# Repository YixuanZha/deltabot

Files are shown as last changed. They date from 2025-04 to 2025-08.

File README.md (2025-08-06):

# The Delta Bot

### What is the Delta Bot?
The Delta Bot is an open-source DIY robot AI platform that uses Radxa's single board computer, the [Rock 5B](https://radxa.com/products/rock5/5b/), a simple [camera module](https://www.raspberrypi.com/products/camera-module-v2/), Parallax's [Continuous Rotation Servo Motors](https://www.parallax.com/product/parallax-continuous-rotation-servo-factory-centered/), and the [RPLIDAR A1](https://www.slamtec.com/en/lidar/a1), a LIDAR camera by Slamtec.

<p align="center">
  b465403a364265f6c7dfb5f9f959081e
</p>

### Purpose & Vision

<p align="center">
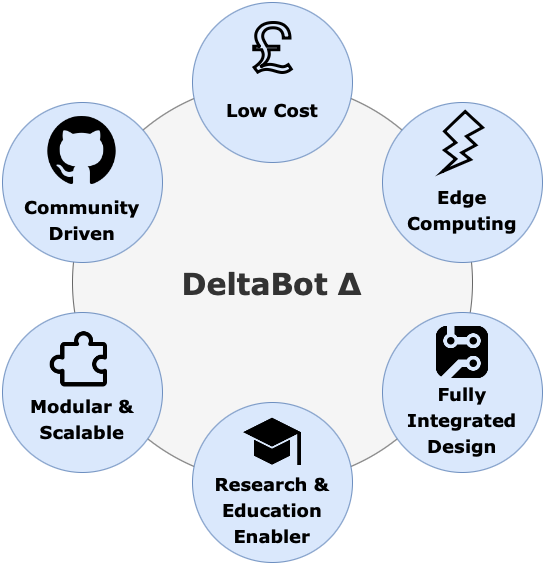
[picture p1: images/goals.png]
Goals
  
</p>

### What can it do?

- 360 Degree 2D LiDAR Scans
- Precise Servo Movement 
- 1080p Video Capture
- Can be configured for Line Following, SLAM, Obstacle Detection, and more!

### Video Demonstration

*A video demonstration will be added once mechanical repairs are complete.*

<p align="center">
  <a href="https://www.youtube.com/watch?v=VIDEO_ID">
    Watch the video
  </a>
</p>

## How to get started
- For the list of components used refer to [List.md](List.md).
- To first set up your RADXA ROCK5B computer, and configure its GPIO pins refer to [Setup.md](Setup.md).
- For details on the DeltaBot schematic, pcb, and footprint library refer to [PCB.md](PCB.md).

### Installing core tools
```bash
sudo apt install libopencv-dev opencv-data python3-opencv
sudo apt install opencl-headers ocl-icd-opencl-dev
sudo apt install libgstreamer1.0-dev gstreamer1.0-plugins-base gstreamer1.0-plugins-good gstreamer1.0-tools
```
### Build the project
```bash
mkdir build
cd build
cmake ..
make
```

### Run the tests
If you want to test the wheels
```bash
./TestServoMotor <left_speed> <right_speed>
```
- `<left_speed>`: Speed value for the left servo motor(-10~10)
- `<right_speed>`: Speed value for the right servo motor(-10~10)
- `speed range`: -10 is full speed counterclockwise, 10 is full speed clockwise, 0 is no rotation
or
```bash
./TestSpeedChange
```
This test will demonstrate the motors accelerating, decelerating, and stopping automatically.

If you want to test the robot's movement
```bash
./TestBotMotion
```
This test allows you to control a robot using your keyboard in a terminal environment. You can drive the robot forward, backward, turn, adjust speed, stop, and exit the program using designated keys.
#### Controls
| Key | Action |
|-----|---|
| W | Forward |
| S | Backward |
| A | Turn Left |
| D | Turn Right |
| R | Speed Up |
| F | Decelerate |
| X | Stop |
| Z | Quit |

#### Example

```text
Use the keyboard to control the bot: W(forward) S(backward) A(turn left) D(turn right) R(speed up) F(decelerate) X(stop) Z(quit)
Forward.....The speed is: 3
Turn left.....The speed is: 3
Speed up.....The speed is: 4
Stop.....
Quit.....
```
### Run the executable
```bash
./TestLineFollowing
```
You need to place the robot in a well-lit area with a high-contrast black line (e.g., electrical tape) on a white or light-colored background. The robot will then start its autonomous line-following behavior.

## Structure
The following outlines the DeltaBot's Architecture:
<p align="center">
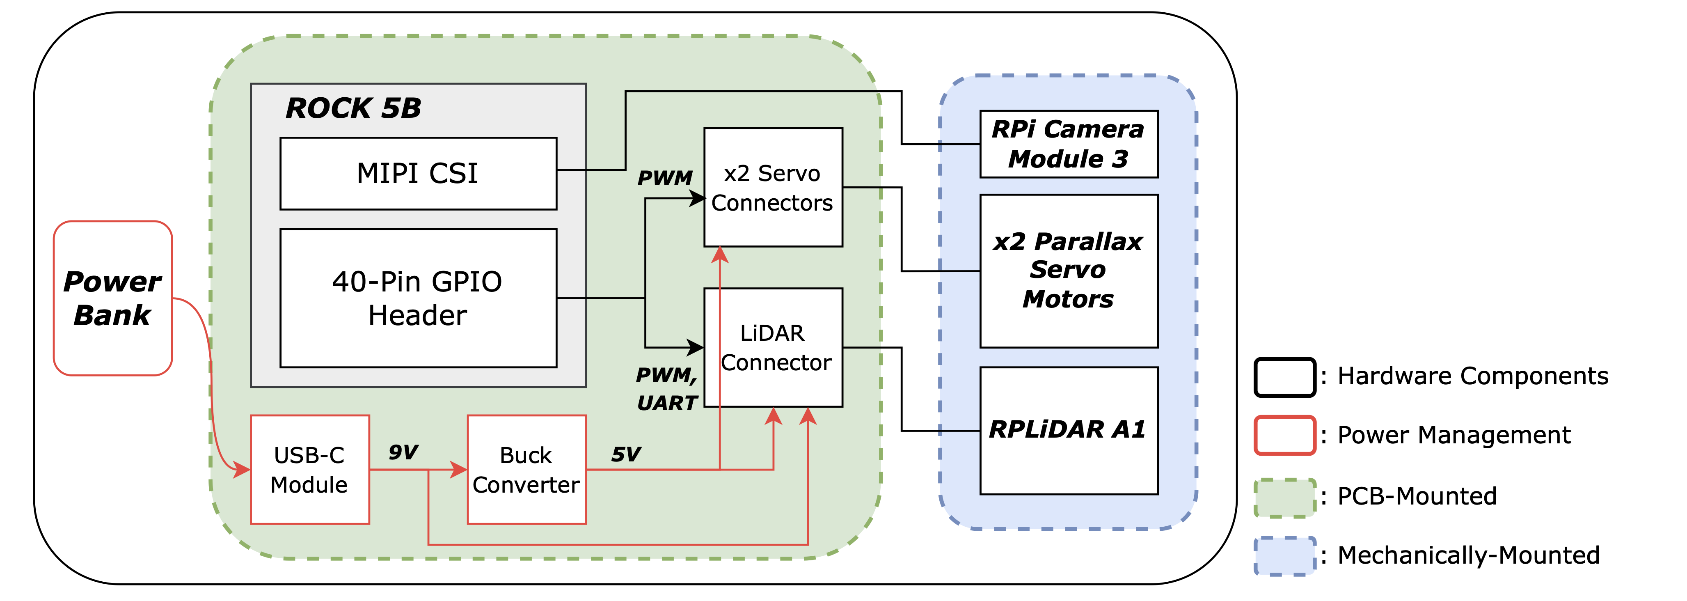
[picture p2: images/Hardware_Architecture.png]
  
</p>

### Additional Mechanical Parts
Additional Mechanical Parts were designed in CAD and can be accessed [here](additional_files/deltabot.f3z).
These were used to secure the external components onto the Single PCB Chassis:
<p align="center">
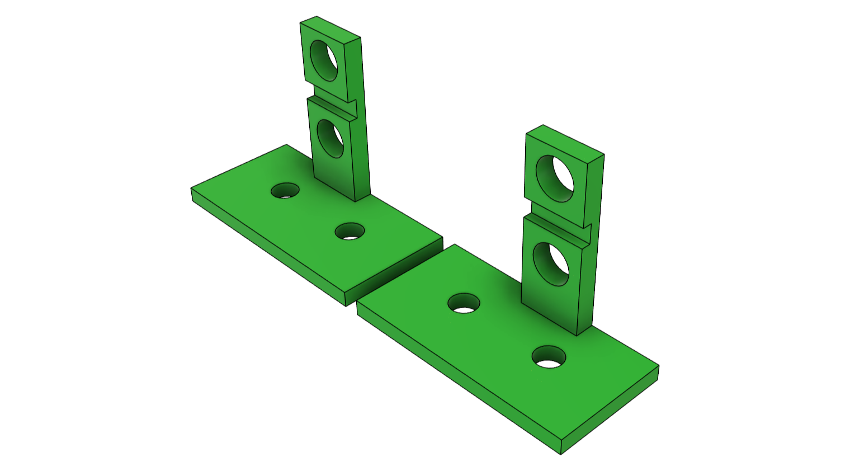
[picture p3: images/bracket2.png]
  
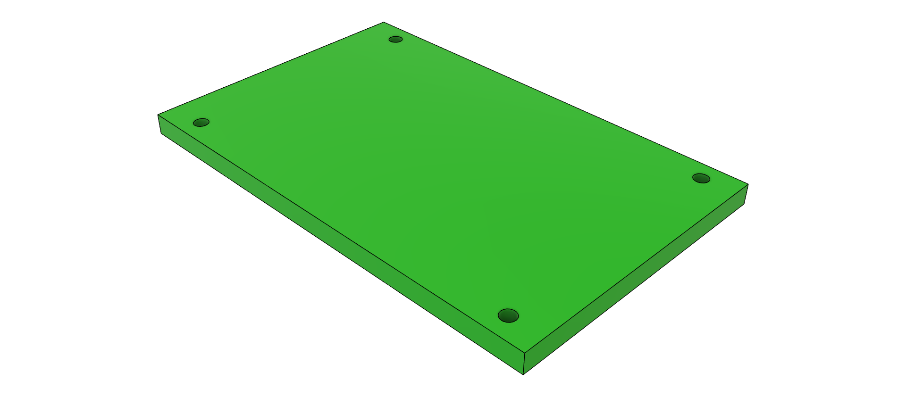
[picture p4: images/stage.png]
  
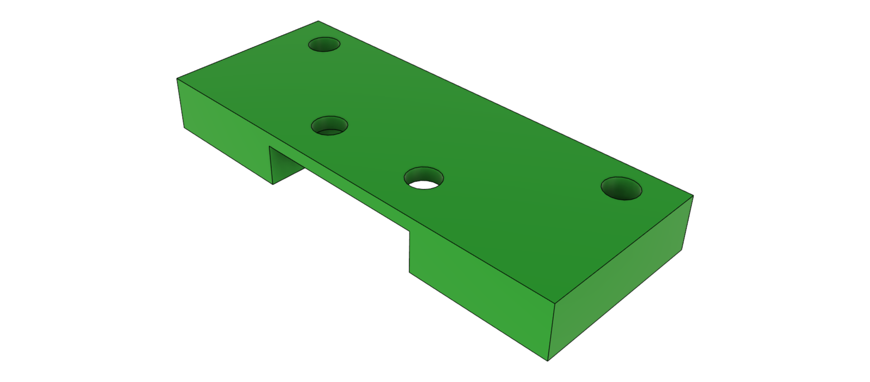
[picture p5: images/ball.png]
  
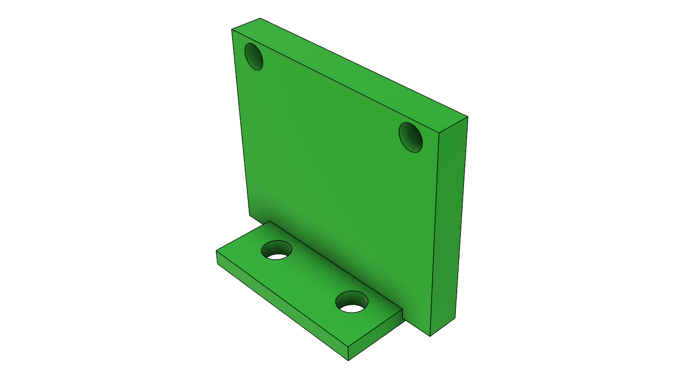
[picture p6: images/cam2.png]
  
</p>

## Further Documentation
- [RADXA ROCK 5B Geekbenchv6 CPU Results](https://browser.geekbench.com/v6/cpu/11503510)
- [RADXA ROCK 5B Geekbenchv6 GPU (OpenCL) Results](https://browser.geekbench.com/v6/compute/4045302)
- Scripts from rplidar_rock file were adopteed from [here.](https://github.com/berndporr/rplidar_rpi)

## Credits
- Saleh AlMulla - 2721704A@student.gla.ac.uk
- Bernd Porr -  bernd.porr@glasgow.ac.uk
- Yixuan Zha - 2974642Z@student.gla.ac.uk

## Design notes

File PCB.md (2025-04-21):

# DeltaBot PCB Overview

The DeltaBot PCB was designed in **KiCad** with a double-sided layer layout. The design integrates key subsystems including the **Radxa ROCK 5B**, LiDAR sensor, camera module, and servo motors.

<p align="center">
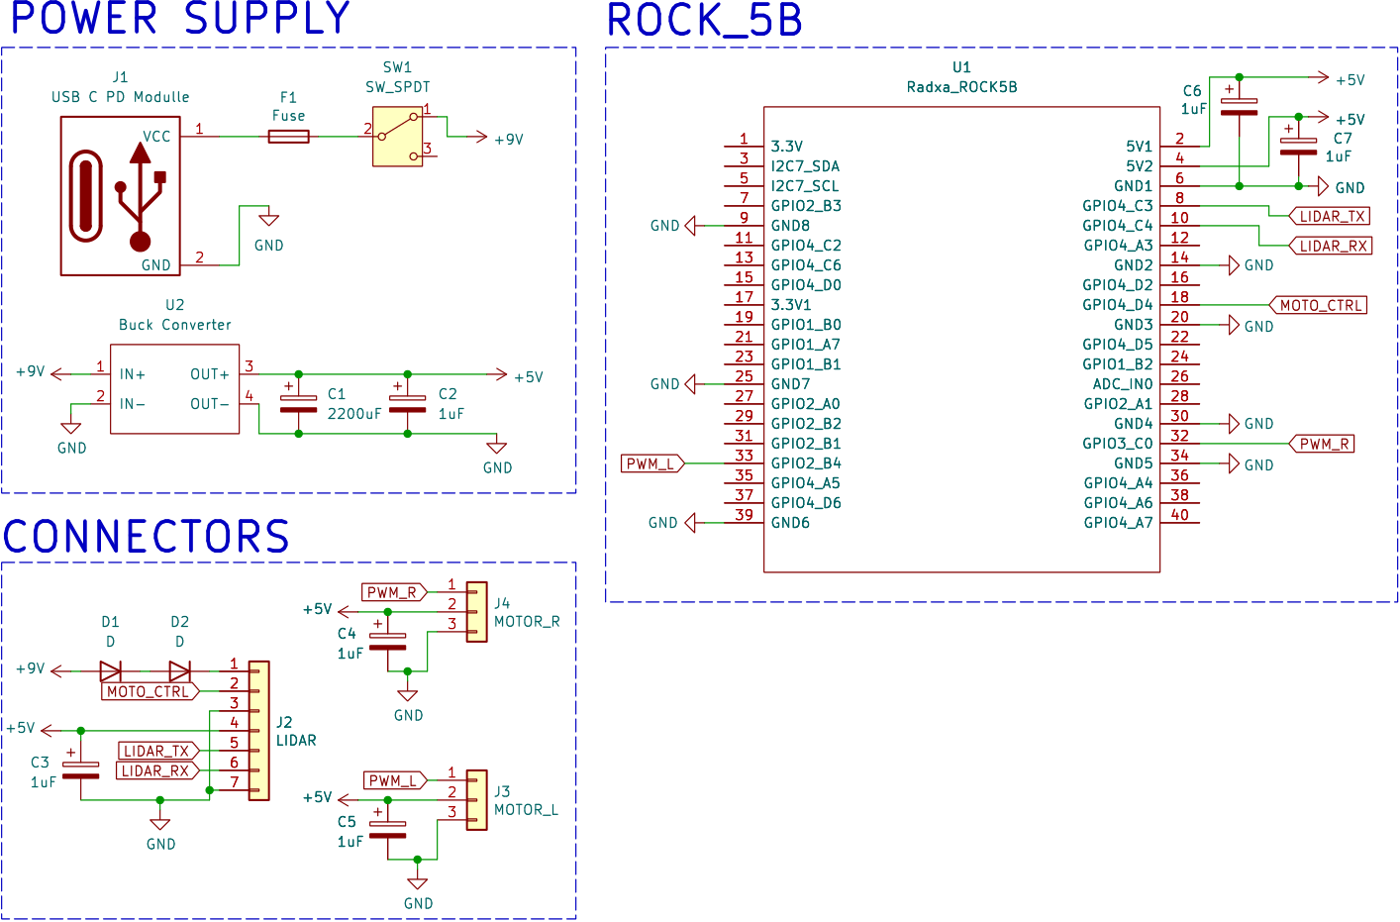
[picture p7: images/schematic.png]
  
</p>

---

## Power System
- Powered via **USB-C Power Delivery (PD)** module at **9V**, stepped down to **5V** using a **DC-DC buck converter**
- A **3.15A fuse** protects against overcurrent
- An **SPDT switch** provides manual ON/OFF control
- A **2200 µF capacitor** suppresses 5V rail ripple for improved voltage stability
- **1 uF** blocking capacitors between each POWER & GND

The following summarizes the power distribution architecture:

<p align="center">
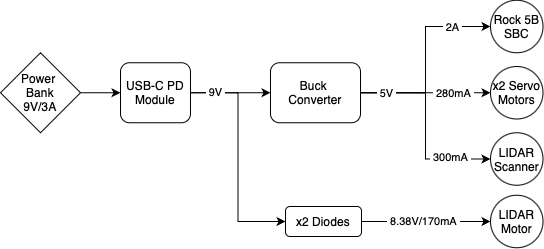
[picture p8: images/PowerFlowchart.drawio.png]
  
</p>

_Note: Current draw listed is based on peak operational requirements._

---

## PCB Layout (Front & Back Layers)

<p align="center">
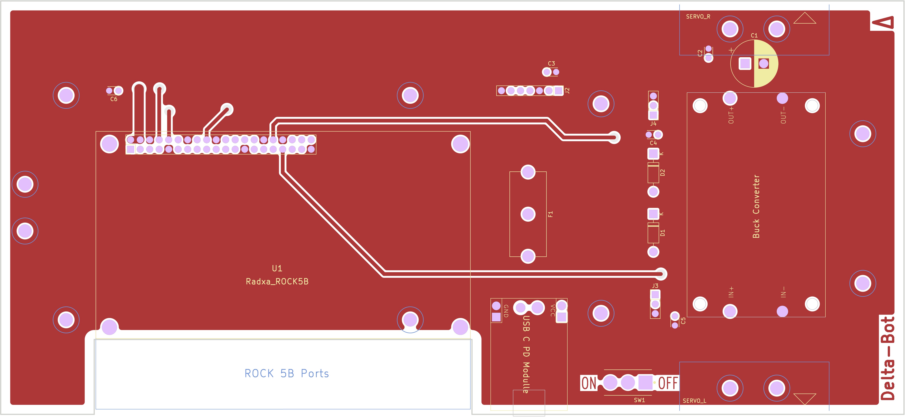
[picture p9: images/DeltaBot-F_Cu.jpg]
  
</p>
<p align="center">
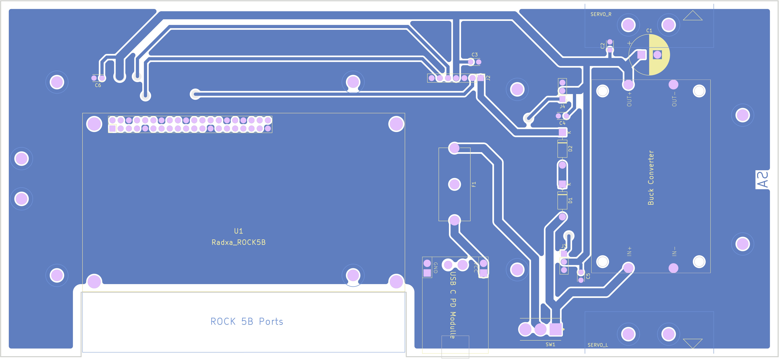
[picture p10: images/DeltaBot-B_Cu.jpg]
  
</p>

---

## ROCK 5B GPIO Pin Assignments

| Function | GPIO Pin(s) | Description |
|---|---|---|
| +5V Power | 2, 4 | Supplies power to board |
| GND | Multiple | Ground reference |
| UART_TX | 8 | TX to LiDAR's RX |
| UART_RX | 10 | RX from LiDAR's TX |
| MOTO_CTRL | 18 | PWM for LiDAR motor |
| PWM_L | 32 | PWM control for left servo |
| PWM_R | 33 | PWM control for right servo |

To change or add to the layout, check [here](https://wiki.radxa.com/Rock5/hardware/5b/gpio) for the rock's gpio connections.

---

## Connectors

- **J2 (LiDAR)**: 7-pin Molex  
  - UART (TX/RX), PWM for motor control, 5V & 8.34V power lines
  - There is a useful image on the LiDAR wiring in the read.me of [this repository](https://github.com/berndporr/rplidar_rpi).
- **J3 / J4 (Servo Motors)**: 3-pin headers  
  - 5V, GND, PWM (Left/Right)

---

## Files

- [Full Schematic](schematic_files/DeltaBot.kicad_sch)
- [PCB Design](schematic_files/DeltaBot.kicad_pcb)
- [PCB Footprints](schematic_files/deltabot.pretty.zip)
- [Rock 5B KiCAD Symbol](schematic_files/deltabot.lib.kicad_sym)
  
---

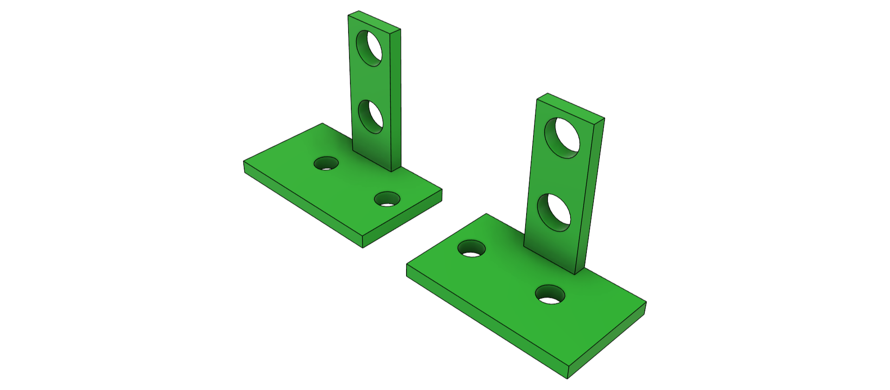
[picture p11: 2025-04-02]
images/bracket.png

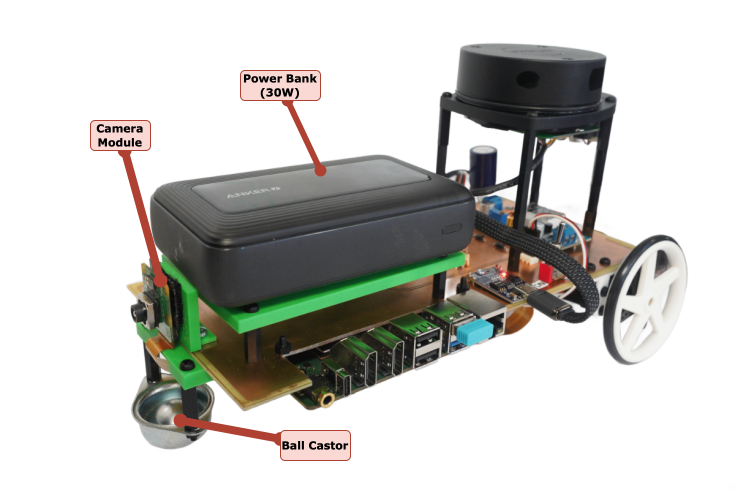
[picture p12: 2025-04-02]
images/frontbot.drawio.png

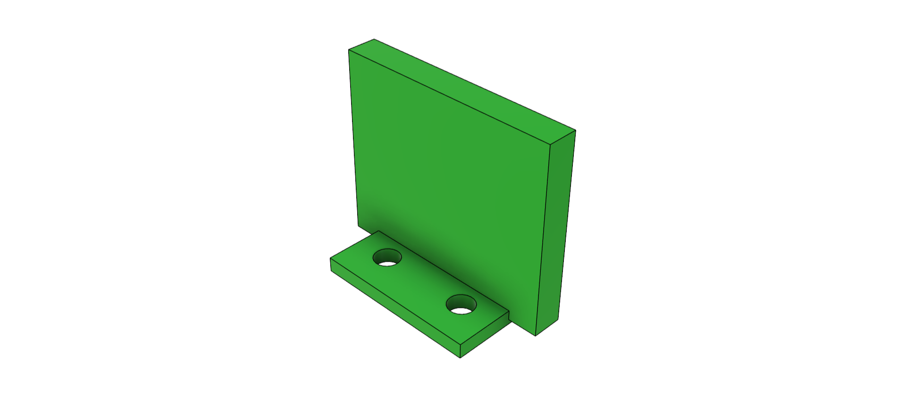
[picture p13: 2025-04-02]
images/cam.png

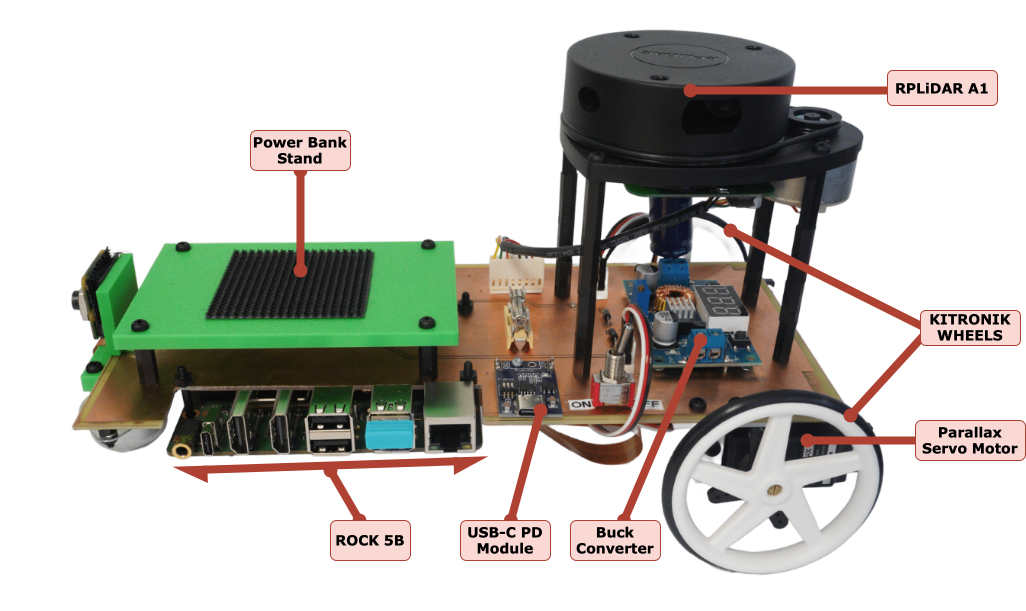
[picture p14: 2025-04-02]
images/sidebot.drawio.png

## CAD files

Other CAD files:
additional_files/deltabot.f3z

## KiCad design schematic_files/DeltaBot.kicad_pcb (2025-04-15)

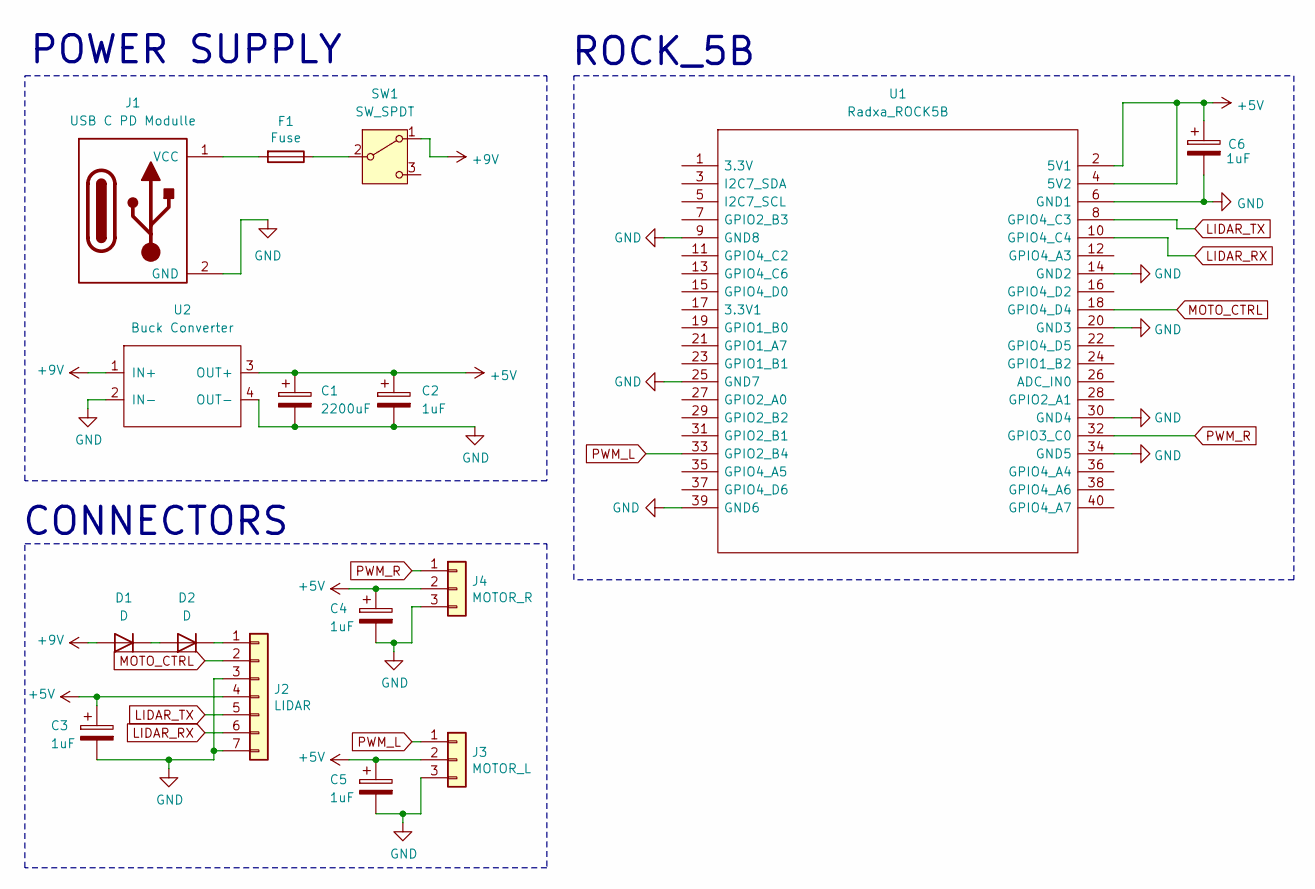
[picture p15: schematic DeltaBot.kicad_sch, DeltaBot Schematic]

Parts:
C1: 2200uF; CP_Radial_D12.5mm_P5.00mm
C2, C3, C4, C5, C6: 1uF; C_Disc_D3.0mm_W2.0mm_P2.50mm
D1, D2: D; D_DO-41_SOD81_P10.16mm_Horizontal
F1: Fuse; Fuseholder_Cylinder-5x20mm_Schurter_0031_8201_Horizontal_Op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
J1: USB C PD Modulle; USB_C
J2: LIDAR; PinHeader_1x07_P2.54mm_Vertical
J3: MOTOR_L; PinHeader_1x03_P2.54mm_Vertical
J4: MOTOR_R; PinHeader_1x03_P2.54mm_Vertical
SW1: SW_SPDT; TE_4-1825136-5
U1: Radxa_ROCK5B; ROCK_5B; Manufacturer_Part_Number ROCK5B V1.3
U2: Buck Converter; BUCK_CONV

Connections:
+5V: C1.1, C2.1, C3.1, C4.1, C5.1, C6.1, J2.4, J3.2, J4.2, U1.2 (5V1), U1.4 (5V2), U2.3 (OUT+)
+9V: D1.2 (A), SW1.1 (A), U2.1 (IN+)
GND: C1.2, C2.2, C3.2, C4.2, C5.2, C6.2, J1.2 (GND), J2.3, J2.7, J3.3, J4.3, U1.6 (GND1), U1.9 (GND8), U1.14 (GND2), U1.20 (GND3), U1.25 (GND7), U1.30 (GND4), U1.34 (GND5), U1.39 (GND6), U2.2 (IN-), U2.4 (OUT-)
LIDAR_RX: J2.6, U1.10 (GPIO4_C4)
LIDAR_TX: J2.5, U1.8 (GPIO4_C3)
MOTO_CTRL: J2.2, U1.18 (GPIO4_D4)
unnamed: D1.1 (K), D2.2 (A)
unnamed: D2.1 (K), J2.1
unnamed: F1.2, J1.1 (VCC)
unnamed: F1.1, SW1.2 (B)
PWM_L: J3.1, U1.33 (GPIO2_B4)
PWM_R: J4.1, U1.32 (GPIO3_C0)

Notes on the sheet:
POWER SUPPLY
CONNECTORS
ROCK_5B

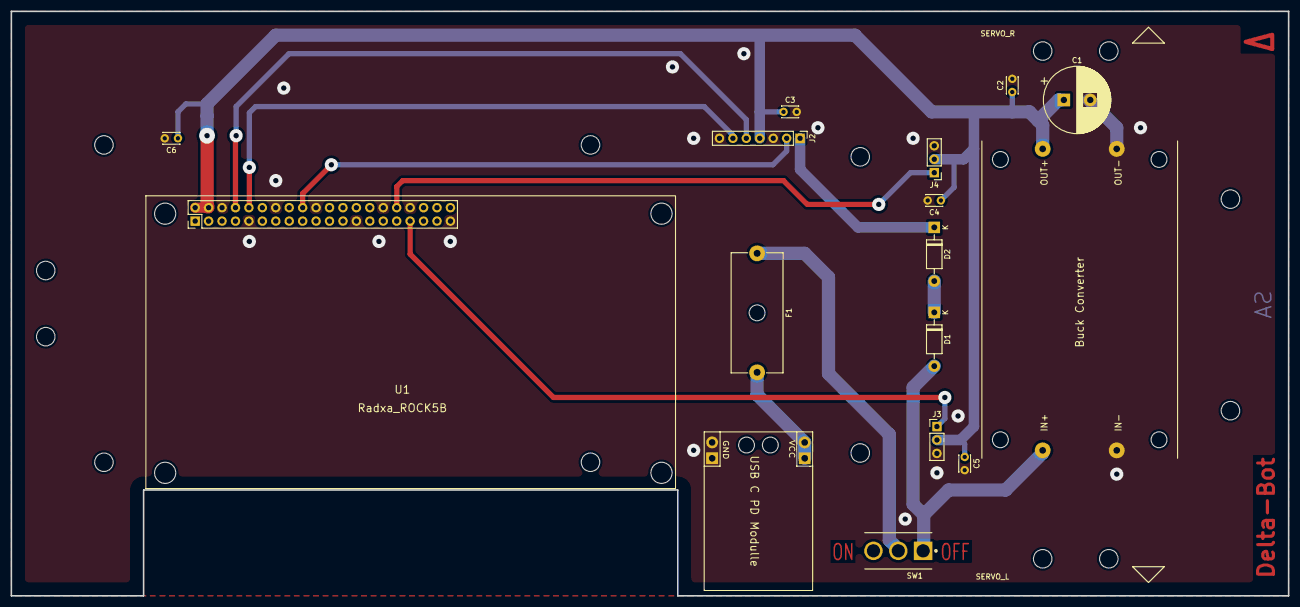
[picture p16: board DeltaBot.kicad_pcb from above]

Board: 2 copper layers, 241.5 x 110.5 mm, 17 parts (0 on the bottom side), 12 nets.

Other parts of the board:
REF\: MountingHole_3.5mm

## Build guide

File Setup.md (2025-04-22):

# Getting Started:

### Items Needed (Requirements):
- Main computer: [RADXA ROCK5B](https://radxa.com/products/rock5/5b/#documentation)
- NVME SSD (any size)
- MicroSD card (any size)
- USB Mouse & Keyboard
- Ethernet Cable & Connection
- HDMI Cable & Display
- USB-C cable with ≥30W Power Adapter

## Installing the System:
Refer to [RADXA official 'Getting Started' Page](https://docs.radxa.com/en/rock5/rock5b/getting-started).

Image Downloads: [Summary of resource downloads](https://docs.radxa.com/en/rock5/rock5b/download).

### In short, 
- Use a MicroSD card as a boot disk to flash the system’s SPI.
  - Download & Open [balenaEtcher](https://etcher.balena.io/#download-etcher) to burn the specific image you want to use (in this case Debian was used).
- Boot up your device and login - User: radxa | Password: radxa
- Copy the Image file from the MicroSD card into the NVME. Refer to [this page](https://docs.radxa.com/en/rock5/rock5b/getting-started/install-os/nvme).

If done successfully, power off the system, remove the MicroSD card, and the system should boot from the NVME drive.

### Troubleshooting tips:
- Run `lsblk` in the command line, and it should output something like this if steps were done correctly:
```
NAME        MAJ:MIN RM   SIZE RO TYPE MOUNTPOINT
mtdblock0    31:0    0    16M  0 disk 
zram0       254:0    0   3.9G  0 disk [SWAP]
nvme0n1     259:0    0 238.5G  0 disk 
├─nvme0n1p1 259:1    0    16M  0 part /config
├─nvme0n1p2 259:2    0   300M  0 part /boot/efi
└─nvme0n1p3 259:3    0 238.2G  0 part /
```
  - Names `mmcblkXpY` are for SD card partitions | `nvmeXbYpZ` for NVME SSD partitions.
  - The device with `/boot/efi` under the MOUNTPOINT column is your root filesystem and boot device.

- Make sure to use the correct path when copying the system image onto the NVME and replace `radxa@192.167.2.66` with the correct username and IP address for you ROCK 5B board.
  - You can find your IP address of your board by running `ip addr show` on the command line.
    - This will display the network interfaces and their IP addresses. Look `inet` followed by an address like `192.167.x.x` or `127.x.x.x`.

## Configure the PWM pins:

The ROCK5B exposes multiple PWM-capable pins. First enable the PWM controller and channel via the sysfs interface.

### Step 1: Activate Pins Using `r-setup`

[`r-setup`]([https://github.com/radxa/rsetup](https://docs.radxa.com/en/rock5/rock5c/radxa-os/rsetup)) is a utility by Radxa to simplify GPIO, I2C, SPI, and PWM configuration. Use it to configure pins to their correct function.

### Step 2: Export & Set PWM

export the correct PWM channel using sysfs. For PWM5_M2, it is pwmchip5, channel 0:

`echo 0 | sudo tee /sys/class/pwm/pwmchip5/export`

`ls /sys/class/pwm/pwmchipX/pwmY` to list activated pins and check if export worked.

pwmchipX → The PWM controller (varies based on hardware)
pwmY → The PWM channel within that controller

Let's use Pin 18, ie. PWM5_M2 for example:

`echo 0 | tee /sys/class/pwm/pwmchip5/export`

You can manually set the PWM signal by

```
echo 20000000 | tee /sys/class/pwm/pwmchip5/pwm0/period
echo 1500000 | tee /sys/class/pwm/pwmchip5/pwm0/duty_cycle
echo 1 | tee /sys/class/pwm/pwmchip5/pwm0/enable
```

#### Note:
Parallax Continuous Rotation Servo Motors require a pulse range of 1.3-1.5ns and a 20ms pause between every pulse:
- A pulse duration of 1.5 ms corresponds to a neutral position.
- A pulse duration below 1.5 ms induces clockwise rotation.
- A pulse duration above 1.5 ms, induces counterclockwise rotation.

### Step 3: C++ Integration
All the code scripts are found in [scripts](scripts).
Including the Servo [test script](scripts/pwm_test.cpp).

## Setting up the LIDAR (pending full integration)

1. **Connect the RPLIDAR A1** to the ROCK5B using UART on `/dev/ttyS2`:
   - TX from the LIDAR → GPIO10 (RX on ROCK5B)
   - RX from the LIDAR → GPIO8 (TX on ROCK5B)

2. Configure pins:
   - Use rsetup to turn on the UART2_M2 and PWM_5 on the ROCK 5B

3. Configure pins:
   - Build the [rplidar_rock](scripts/rplidar_rock).
```
mkdir build && cd build
cmake ..
make -j$(nproc)
```
4. Run the demo:
  - Test LIDAR startup and initialization by running `./printdata`

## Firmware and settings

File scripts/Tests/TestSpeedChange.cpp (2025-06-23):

#include "ServoMotorSetting.h"
#include <thread>
using namespace std;

// This program gradually increases the speed of two servo motors from -10 to 10.
// The speed is changed every second, and the final speed is printed to the console.

int main(int argc, char* argv[])
{
    ServoMotorSetting servo_right(0, 20, 1.52, 14); // 1.5ms
    ServoMotorSetting servo_left(0, 20, 1.52, 8); // 1.5ms

    int speed = -10;

    for(int i = 0; i <= 20; i++)
    {
        servo_left.ChangeLeftSpeed(speed);
        servo_right.ChangeRightSpeed(speed);
        cout << "The speed is: " << speed << endl;
        speed ++;
        std::this_thread::sleep_for(std::chrono::seconds(1));
    }
    servo_left.StopMotor();
    servo_right.StopMotor();

    return 0;
}

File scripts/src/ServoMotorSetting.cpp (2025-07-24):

#include "ServoMotorSetting.h"

ServoMotorSetting::ServoMotorSetting(int channel, float low_time, float high_time, int chipNo)
{
    pwm.StartPWM(channel, low_time, high_time, chipNo);
}

ServoMotorSetting::~ServoMotorSetting()
{
    pwm.disable();
}

int ServoMotorSetting::SpeedToHighTimeLeft(float speed) // speed range from -10 to 10, 0 is stop
{
    if (speed > 10)
        speed = 10;
    if (speed < -10)
        speed = -10;
    int neutral_time = 1524000; // When speed is 0, The high time is 1524000
    int step_size = 10000;

    return neutral_time + (speed * step_size);
}

int ServoMotorSetting::SpeedToHighTimeRight(float speed) // speed range from -10 to 10, 0 is stop
{
    if (speed > 10)
        speed = 10;
    if (speed < -10)
        speed = -10;
    int neutral_time = 1521000; // When speed is 0, The high time is 1521000
    int step_size = 10000;

    return neutral_time + (speed * step_size);
}


void ServoMotorSetting::ChangeLeftSpeed(float speed)
{
    int high_time = SpeedToHighTimeLeft(speed);
    int per = INVERSEDUTY + high_time;
    pwm.SetPeriod(per);
    pwm.SetDutyCycleNS(INVERSEDUTY);
}

void ServoMotorSetting::ChangeRightSpeed(float speed)
{
    int high_time = SpeedToHighTimeRight(speed);
    int per = INVERSEDUTY + high_time;
    pwm.SetPeriod(per);
    pwm.SetDutyCycleNS(INVERSEDUTY);
}

void ServoMotorSetting::StopMotor()
{
    ChangeLeftSpeed(0);
    ChangeRightSpeed(0);
}

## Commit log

2025-04-02 servo test code
2025-04-02 Updated bracket and camera
    [rock 5B v1.f3z]
2025-04-02 Rename rock 5B v1.f3z to additional_files/rock 5B v1.f3z
    [rock 5B v1.f3z]
2025-04-15 Schematic minor fixes
    rearranged silkscreen, added capacitors to the pcb
    [DeltaBot.kicad_pcb, DeltaBot.kicad_sch]
2025-04-15 added gbr and drl files
    [DeltaBot-NPTH-drl_map.gbr, DeltaBot-NPTH.drl, DeltaBot-PTH-drl_map.gbr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]
2025-04-20 adjusted labeling
    [DeltaBot.kicad_sch]
2025-04-21 Update PCB.md
    updated pcb image
2025-06-11 Remove PWM test scripts for cleanup
2025-06-11 Implement DeltaBot control and PWM functionality with servo motor settings
2025-06-23 Add CaptureCameraFeed class for camera feed handling
2025-06-23 Fix frame flipping in CaptureCameraFeed::run for correct display orientation
2025-06-23 Remove frame flipping from CaptureCameraFeed::run to maintain original orientation
2025-06-23 Fix frame flipping direction in CaptureCameraFeed::run for correct display orientation
2025-06-23 Update CaptureCameraFeed::run to display resized frames instead of original frames
2025-06-23 Fix neutral time calculation in SpeedToHighTime for accurate speed mapping
    [ServoMotorSetting.cpp]
2025-06-23 Fix neutral time value in SpeedToHighTime for accurate speed mapping
    [ServoMotorSetting.cpp]
2025-06-23 Refactor servo motor speed control methods for clarity and accuracy
2025-06-29 Refactor CaptureCameraFeed class to improve camera initialization and frame processing
2025-06-29 Refactor main function in TestCamera to enhance camera initialization and error handling
2025-06-30 Add camera functionality to DeltaBot class and improve initialization
2025-06-30 Refactor TestCamera to utilize DeltaBot for camera functionality and remove unused CaptureCameraFeed parameters.
2025-07-02 Refactor CaptureCameraFeed class to implement thread control for video capture and add stop functionality
2025-07-02 Implement threading for camera operations in DeltaBot class, adding StartCamera and StopCamera methods for better resource management.
2025-07-02 Add TestBotAndCamera to control DeltaBot and manage camera feed
2025-07-02 Add Threads package requirement and link to TestBotAndCamera executable
2025-07-09 Enhance CaptureCameraFeed class with thread-safe frame handling and error checks for captured frames
2025-07-09 Add SetMotorSpeed method to DeltaBot for controlling motor speeds
2025-07-11 Fix speed initialization in LineFollower to 1.0f
    [LineFollower.h]
2025-07-11 Refactor motor control methods to use SetMotorSpeed for consistency
2025-07-17 Refactor DeltaBot constructor to use unique_ptr for camera management and update StartCamera and StopCamera methods for proper camera handling
2025-07-17 Initialize DeltaBot with camera in TestLineFollowing for proper camera integration
2025-07-17 Fix camera ID initialization in TestLineFollowing to 11 for correct camera feed
2025-07-17 Fix learning rate initialization in LineFollower to 0.001 for improved training accuracy
    [LineFollower.h]
2025-07-17 Fix backpropagation injection layers in UpdateAndTrain for improved training accuracy
    [LineFollower.cpp]
2025-07-18 Update base speed, steering gain, and error gain in LineFollower for improved performance
    [LineFollower.h]
2025-07-18 Refactor speed adjustment and error amplification in UpdateAndTrain for improved control responsiveness
    [LineFollower.cpp]
2025-07-23 Fix typo in binary threshold variable name and correct error amplification calculation in LineFollower
    [LineFollower.cpp, LineFollower.h]
2025-07-24 Update learning rate and error gain in LineFollower for improved training performance
    [LineFollower.h]
2025-07-24 Refactor error propagation in UpdateAndTrain for improved training accuracy
    [LineFollower.cpp]
2025-07-24 Refactor error handling in UpdateAndTrain to improve backpropagation accuracy
    [LineFollower.cpp]
2025-07-24 Refactor neural network output handling in LineFollower for improved steering adjustments and error reporting
    [LineFollower.cpp]
2025-07-24 Refactor backpropagation injection layers in UpdateAndTrain for enhanced error handling
    [LineFollower.cpp]
2025-07-24 Refactor steering adjustments in LineFollower to implement PID control for improved accuracy
2025-07-24 Refactor PID constants in LineFollower for improved control accuracy
2025-07-24 Refactor LineFollower to enhance neural network initialization and improve error handling in line tracking
    [LineFollower.cpp]
2025-07-24 Add CameraFPSTracker class to monitor and report camera feed FPS
2025-07-24 Refactor CaptureCameraFeed class to remove FPS calculation and display methods, streamline frame handling, and improve error handling during frame capture
2025-07-24 Integrate CameraFPSTracker into LineFollower for FPS monitoring and enhance frame processing with flipping and FPS display
    [LineFollower.cpp, LineFollower.h]
2025-07-24 Refactor ServoMotorSetting to clarify neutral time comments and correct documentation for speed-to-high time calculations
    [ServoMotorSetting.cpp]
2025-07-25 Update heading gain in LineFollower for improved control stability
    [LineFollower.h]
2025-07-25 Adjust ROI segment positions in ProcessFrameAndGetInputs for improved frame analysis
2025-07-25 Adjust base speed in LineFollower for improved responsiveness and update ROI segment positions for better frame analysis
2025-07-25 Fix base_speed initialization in LineFollower for correct float representation
    [LineFollower.h]
2025-07-26 Comment out heading error integral calculations in LineFollower for simplified control logic
    [LineFollower.cpp, LineFollower.h]
2025-07-26 Comment out heading error integral calculations in LineFollower to simplify control logic
    [LineFollower.cpp]
2025-07-26 Refactor heading error integral calculations in LineFollower for improved control logic
    [LineFollower.cpp, LineFollower.h]
2025-07-26 Set integral_gain to 0.0f in LineFollower for improved control stability
    [LineFollower.h]
2025-07-26 Revert base speed to 2.0f for line following adjustments
    [LineFollower.h]
2025-07-26 Add last_process_frame_id to track frame processing in LineFollower
2025-07-26 Initialize frame_id in CaptureCameraFeed and update its value during frame capture
2025-07-28 Adjust controller gains for improved line following stability
    [LineFollower.h]
2025-07-28 Replace binary thresholding with adaptive thresholding for improved frame processing
    [LineFollower.cpp]
2025-07-28 Refactor frame processing to use HSV color space for improved binary image generation
2025-07-28 Adjust upper black threshold in HSV color space for improved frame processing
2025-07-28 Refine upper black threshold in HSV color space and add morphological closing to improve frame processing
2025-07-29 Refine upper black threshold in HSV color space for improved frame processing
2025-07-29 Add comments to clarify frame ID tracking and FPS calculation methods
2025-07-30 Use float to replace double
    [LineFollower.cpp, LineFollower.h]
2025-07-30 Update error calculation in UpdateAndTrain method for improved training accuracy
    [LineFollower.cpp]
2025-07-31 Refactor UpdateAndTrain method to simplify error handling and backpropagation logic
    [LineFollower.cpp]
2025-07-31 Fix error_gain value in LineFollower class for improved control response
    [LineFollower.h]
2025-07-31 Fix learning rate value in LineFollower class for improved control response
    [LineFollower.h]
2025-07-31 Fix learning rate and error gain values in LineFollower class for improved control response
    [LineFollower.h]
2025-07-31 Fix proportional gain value in LineFollower class for improved control response
    [LineFollower.h]
2025-07-31 Fix heading gain value in LineFollower class for improved control response
    [LineFollower.h]
2025-07-31 Fix integral gain value in LineFollower class for improved control response
    [LineFollower.h]
2025-07-31 Fix base speed initialization in LineFollower class to use correct float syntax
    [LineFollower.h]
2025-07-31 Update base speed in LineFollower class to correct value for improved performance
    [LineFollower.h]
2025-07-31 Refactor error handling in LineFollower class to simplify processing and improve clarity
    [LineFollower.cpp]
